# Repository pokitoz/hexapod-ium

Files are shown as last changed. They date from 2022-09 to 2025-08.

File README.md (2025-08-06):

# hexapod-ium

An hexapod robot using arduino and servo motors.
Manufacturing (PCB, 3D prints) and component assembly (PCBA) were done with PCBWay: https://www.pcbway.com/.




## Hardware

See the Kicad project in hw/ folder.

There is a Kicad Pluggin (https://www.pcbway.com/blog/News/PCBWay_Plug_In_for_KiCad_3ea6219c.html)
, 
simplifying the order process with PCBWay as the Gerber and BOM are filled in.

The design is reviewed and manufactured rapidely; which was very useful for this project.

### PCB

Kicad was used for the PCB design to add 2xPCA9865 and an ESP32.



### 3D Parts 

3D Printed parts can be done using a Prusa or Bamboo or any other 3d printer like the first iteration. 
But it was simpler to use PCBWay and the quality was better than printing on my own. The parameter used were:
- Resin Standard white material (UTR 8360)
- SLA

Design check and delivery was fast.



### Components

- 6x Leg (3 of them must be mirrored)
- 6x Holder
- 12 servo motors: MG90S or SG90 Micro Servo with screws
- 1 Arduino Uno
- PCA9865 (https://learn.adafruit.com/16-channel-pwm-servo-driver?view=all)
- Blu-tack
- Jumper cables

Need 5V for the motors board. VCC will be propagated to the main board (Arduino, ESP32,..)

You will need at least 2A upper limit to move all the motors at once.

## Software

### Arduino

Basic Arduino program to activate all the servo.
See the pinout in the .ino file. The VCC going out of the PCA9868 should go to the 5V of the board.

### ESP32

Might need driver https://www.silabs.com/developer-tools/usb-to-uart-bridge-vcp-drivers?tab=downloads

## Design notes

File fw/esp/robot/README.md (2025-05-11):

# ESP32 build

Use target: `esp32`, `ESP32-SOLO1-Module`.

Pinout:
- 3v3 and GND to PCA servo board
- SDA 21
- SCL 22



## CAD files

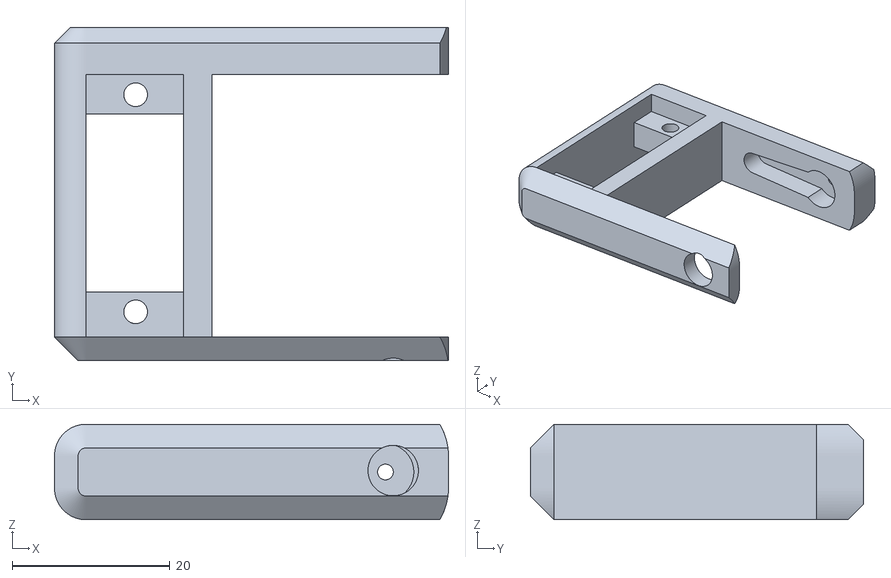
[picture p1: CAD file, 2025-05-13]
3d/Holder Leg.stl
50.0 x 42.3 x 12.1

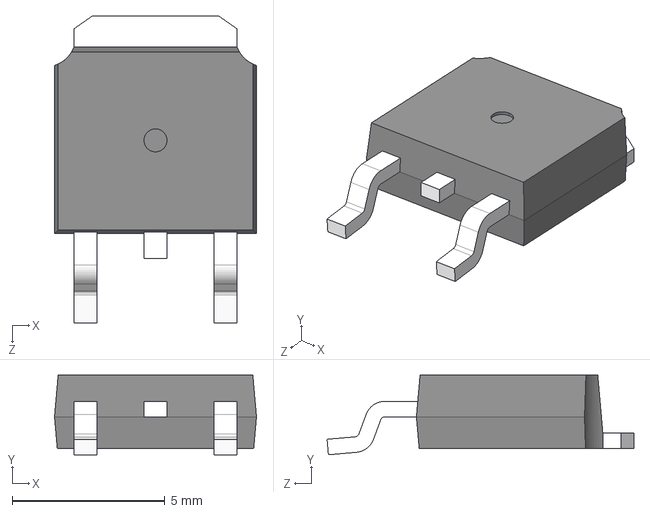
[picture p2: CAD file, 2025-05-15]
hw/AOD417/AOD417.step
6.60 x 2.60 x 10.0 mm

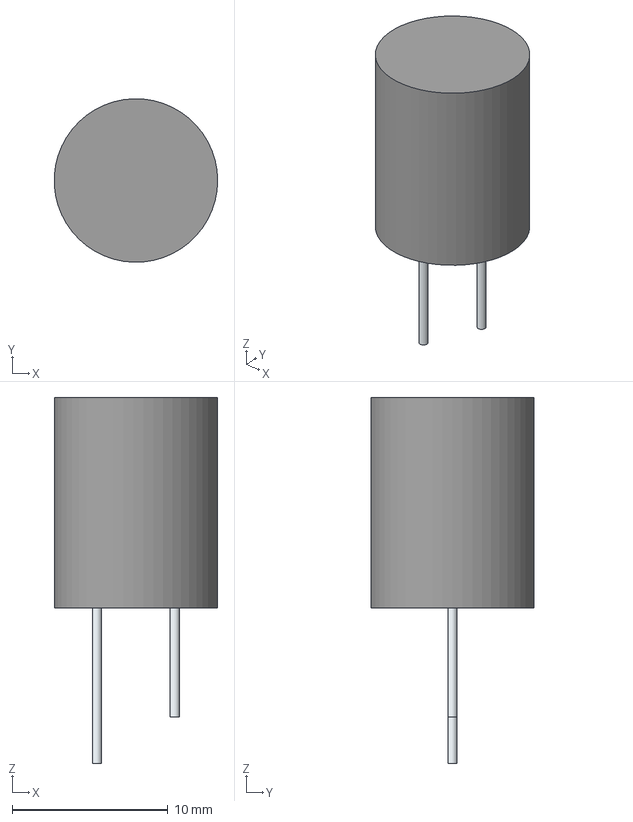
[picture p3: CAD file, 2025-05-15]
hw/ESH108M010AH1AA/3D/ESH108M010AH1AA.stp
10.5 x 10.5 x 23.5 mm
SimpleBody
Pin1
Pin2

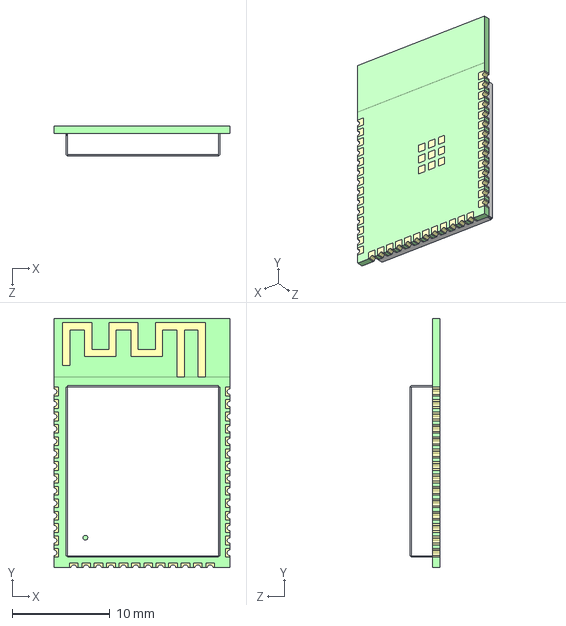
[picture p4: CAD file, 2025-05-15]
hw/ESP32-S3-WROOM-1-N8/3D/ESP32-S3-WROOM-1-N8.stp
18.0 x 25.5 x 3.10 mm

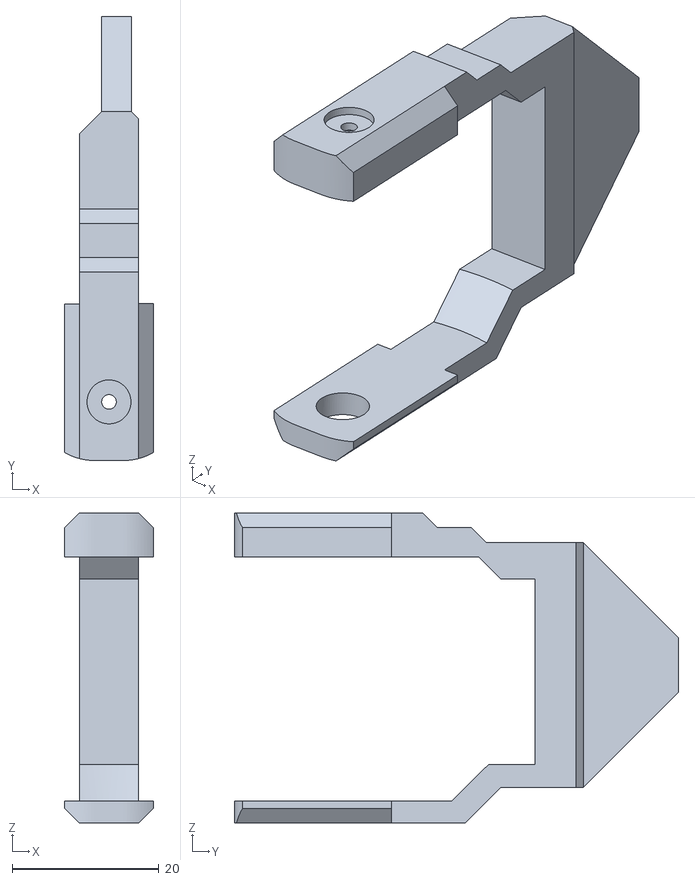
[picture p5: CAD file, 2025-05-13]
3d/Leg_v2.stl
12.1 x 60.6 x 42.3

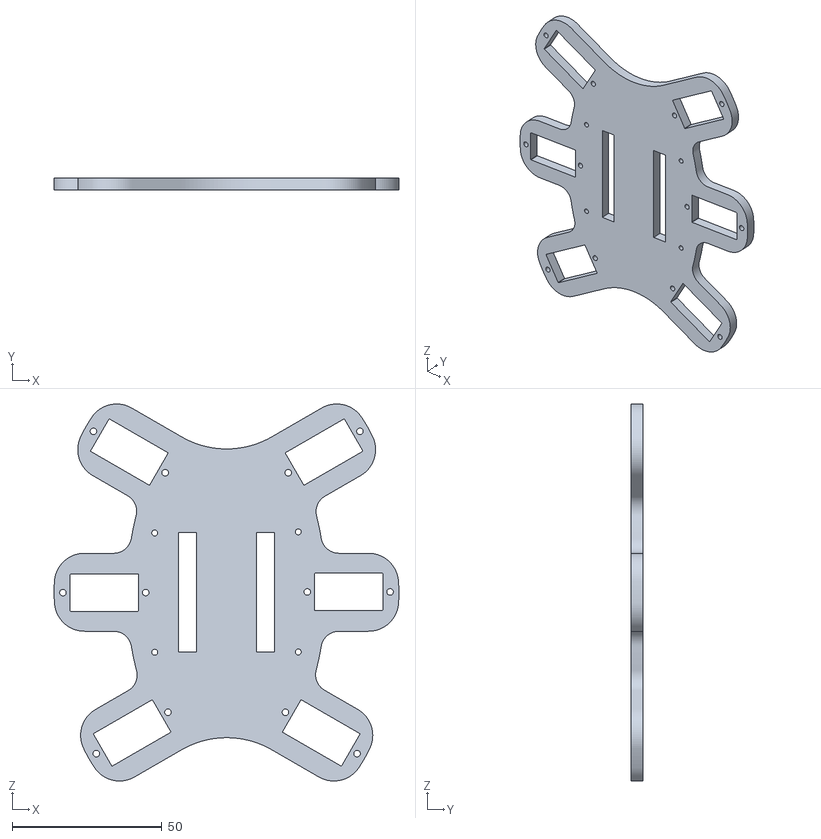
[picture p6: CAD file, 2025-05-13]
3d/BaseDown.stl
115.0 x 4.15 x 125.7

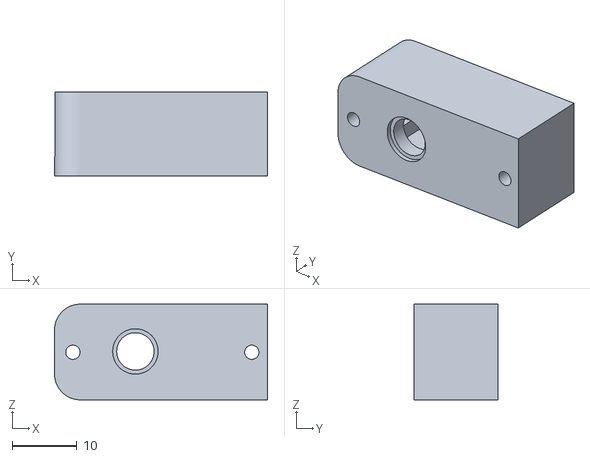
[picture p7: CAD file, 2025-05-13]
3d/ServoHat.stl
32.9 x 13.0 x 14.8

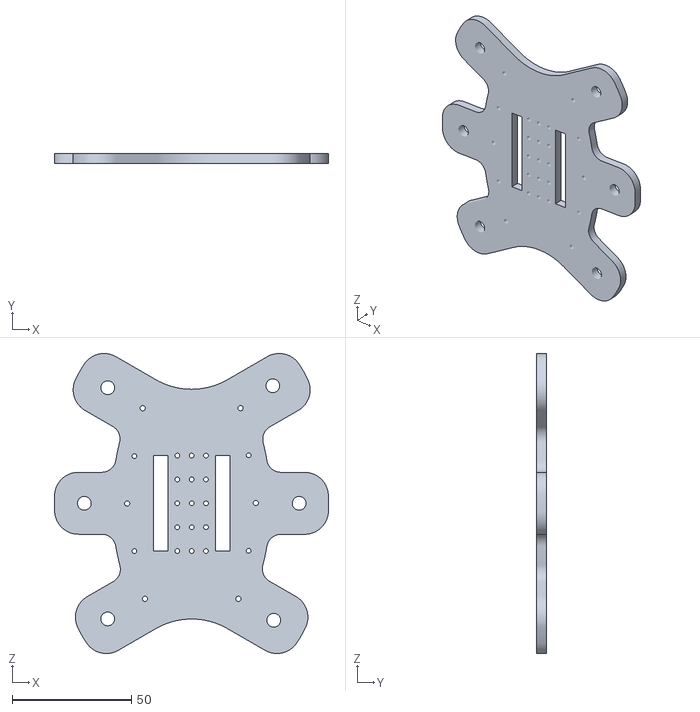
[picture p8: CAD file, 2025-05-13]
3d/Baseup.stl
115.0 x 4.15 x 125.7

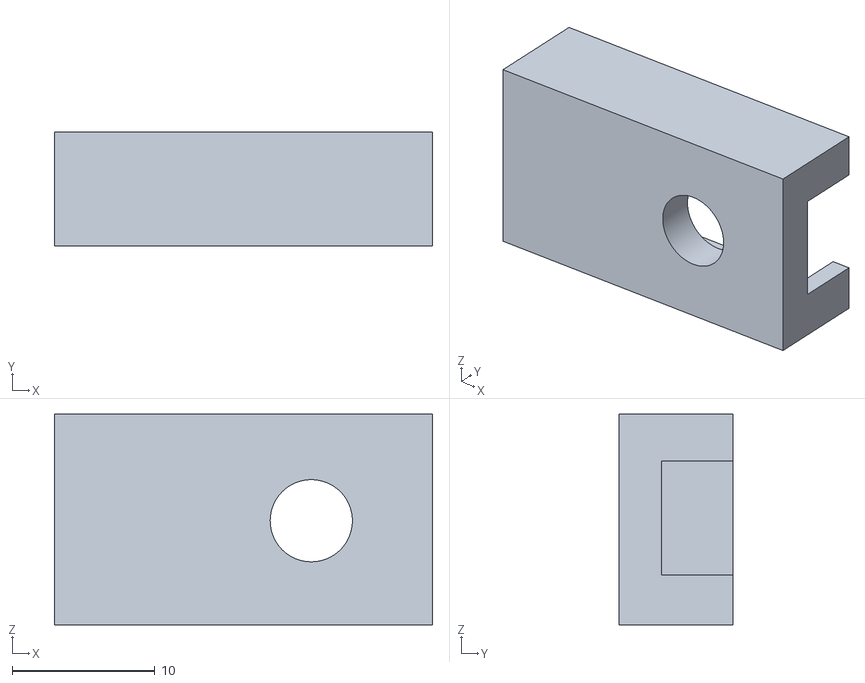
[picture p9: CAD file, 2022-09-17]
3d/Component1.stl
26.5 x 8.00 x 14.8

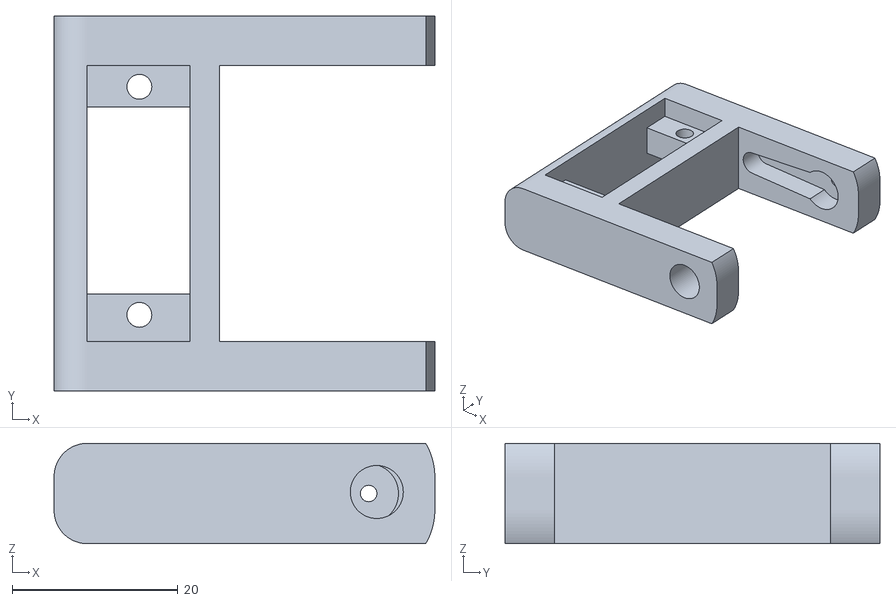
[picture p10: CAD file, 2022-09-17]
3d/Holder.stl
46.0 x 45.3 x 12.1

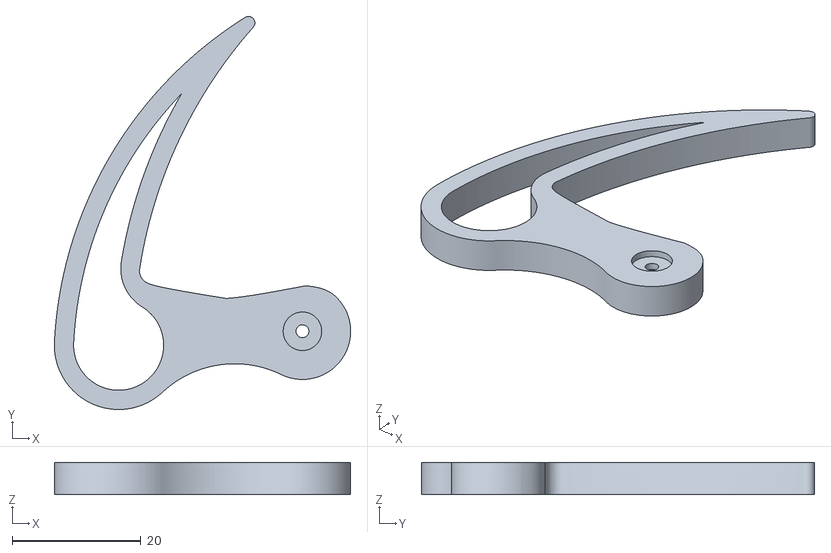
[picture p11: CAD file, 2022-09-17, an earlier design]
3d/Leg.stl
46.1 x 61.1 x 5.00

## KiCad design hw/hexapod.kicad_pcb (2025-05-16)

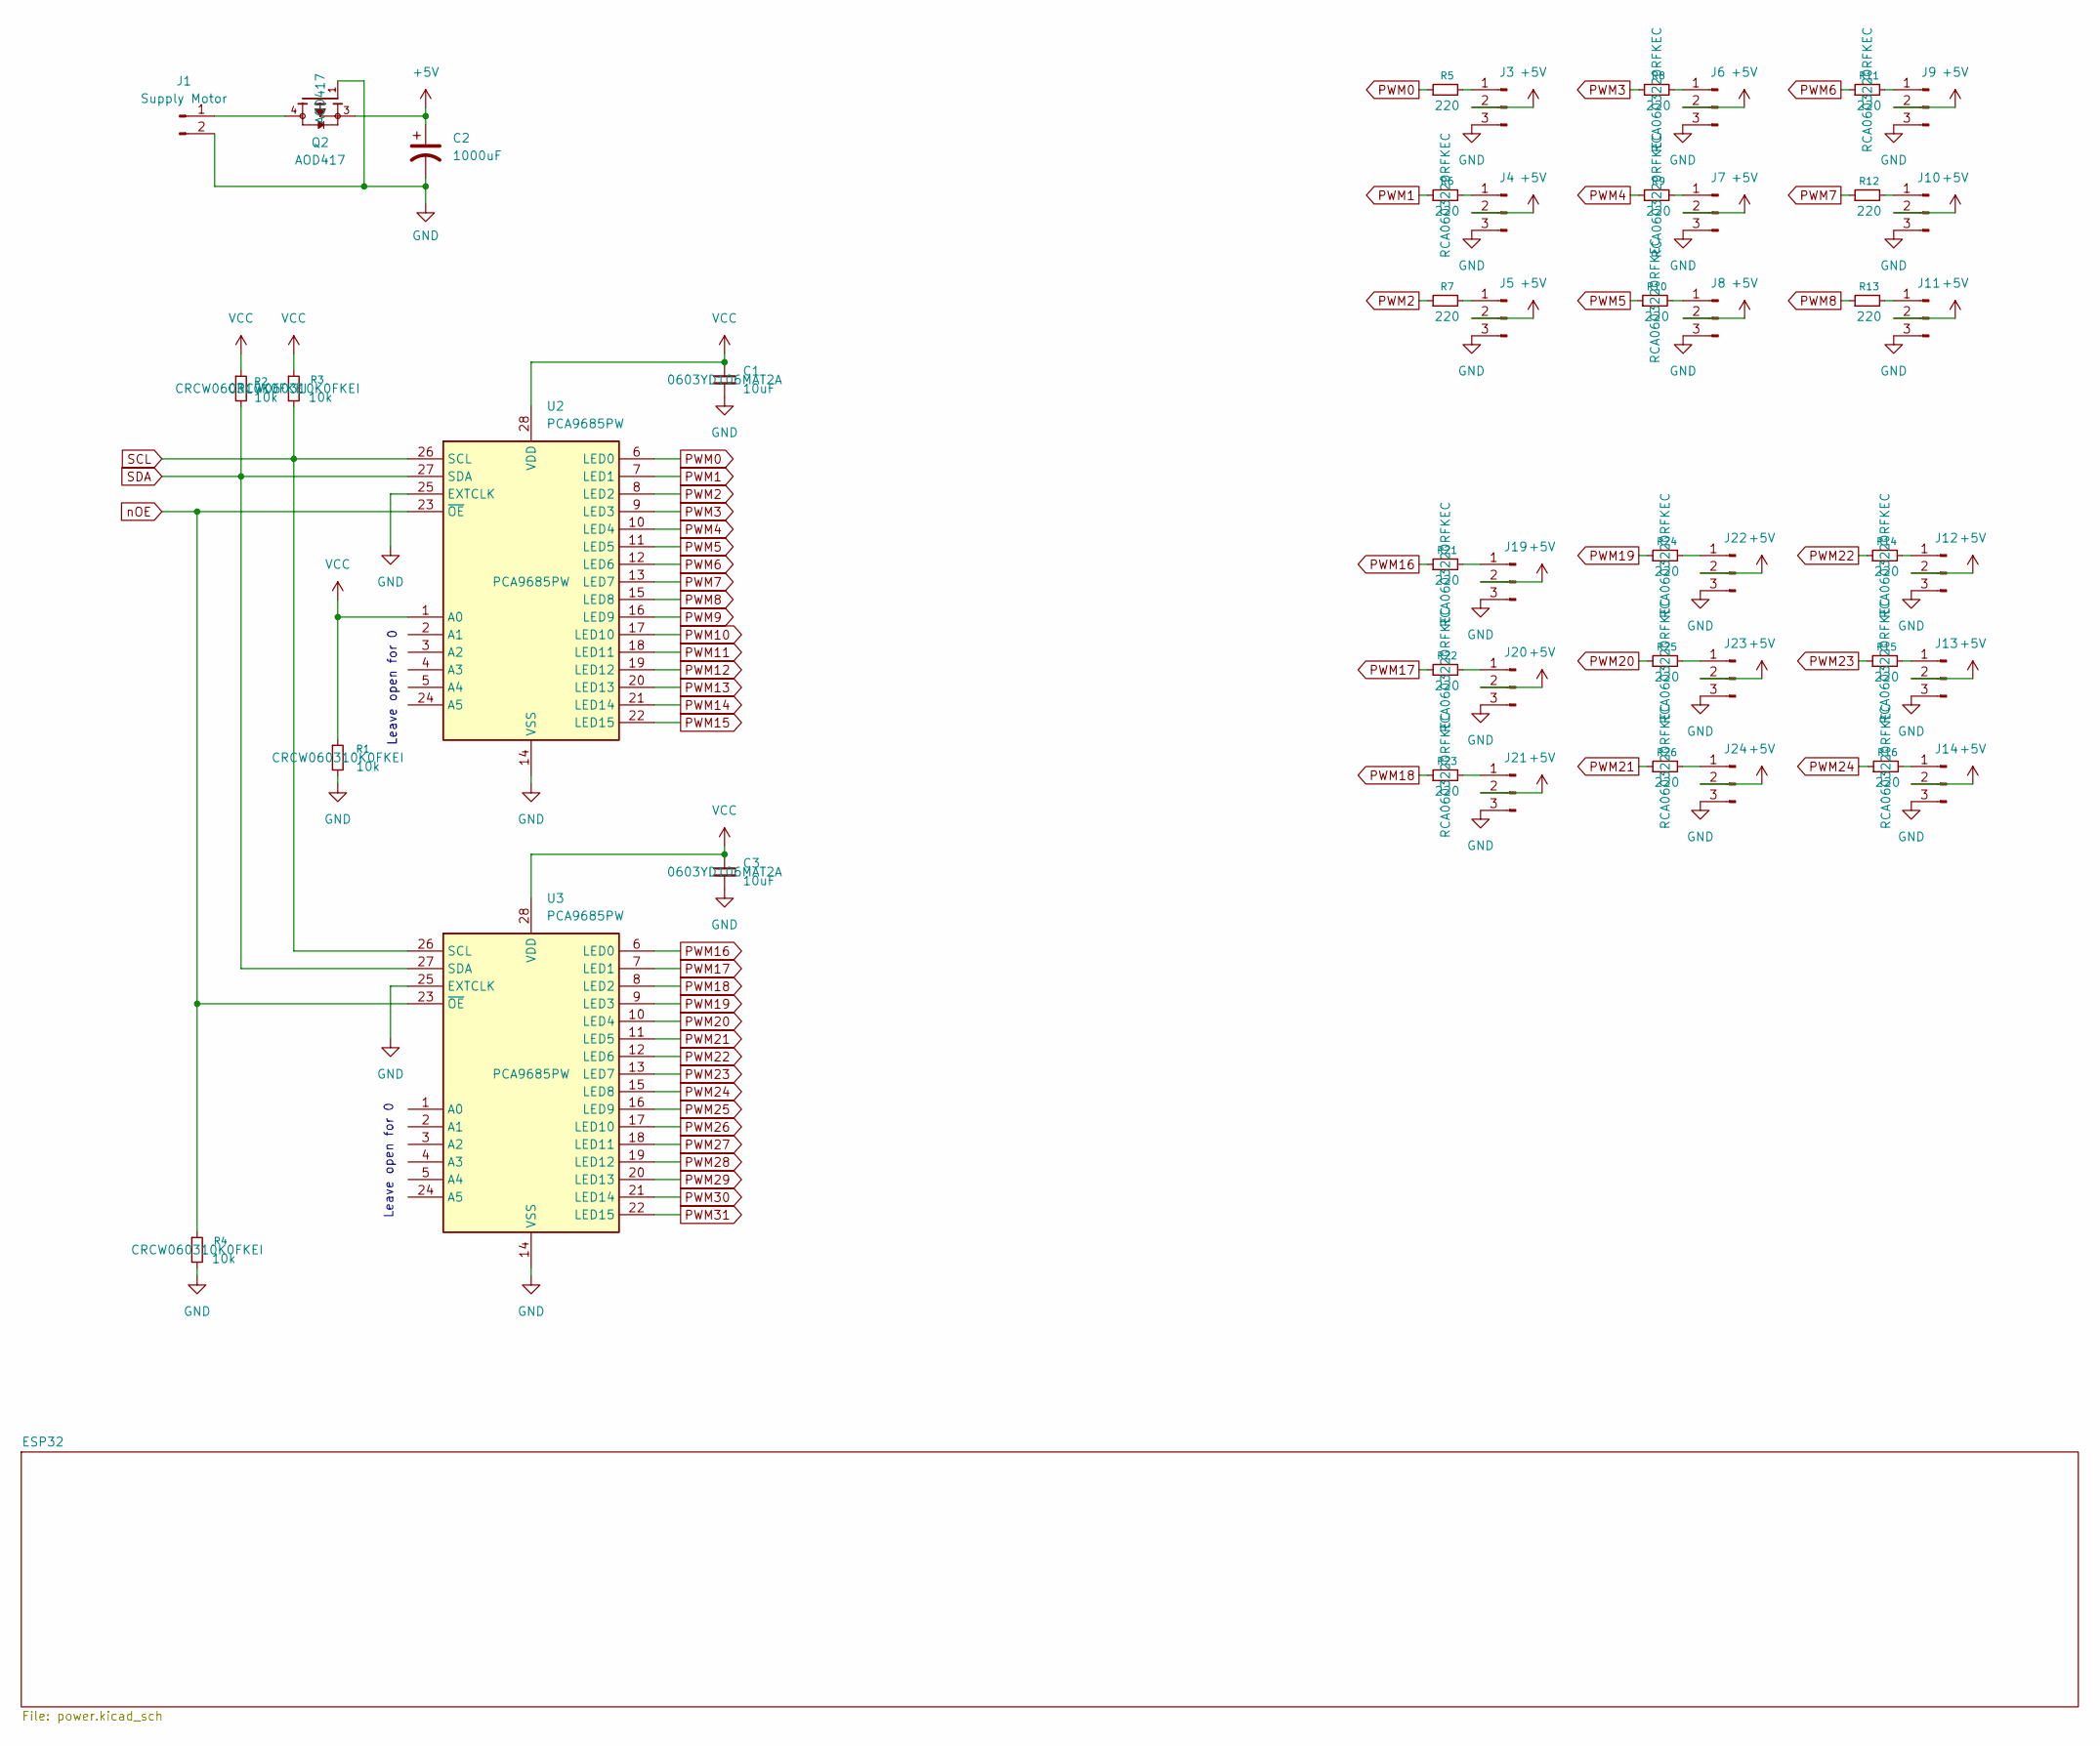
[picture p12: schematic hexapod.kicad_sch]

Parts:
C1, C3: 10uF; C_0603_1608Metric; Part 0603YD106MAT2A
C2: 1000uF; CAPPRD500W60D1000H1350
J1: Supply Motor; AMASS_XT30U-M_1x02_P5.0mm_Vertical
J3, J4, J5, J6, J7, J8, J9, J10, J11, J12, J13, J14, J19, J20, J21, J22, J23, J24: Conn_01x03_Pin; PinHeader_1x03_P2.54mm_Vertical
Q2: AOD417; DPAK228P994X240_3N; PARTREV U
R1, R2, R3, R4: 10k; R_0603_1608Metric_Pad0.98x0.95mm_HandSolder; Part CRCW060310K0FKEI
R5, R6, R7, R8, R9, R10, R11, R12, R13, R14, R15, R16, R21, R22, R23, R24, R25, R26: 220; R_0603_1608Metric_Pad0.98x0.95mm_HandSolder; Part RCA0603220RFKEC
U2, U3: PCA9685PW; TSSOP-28_4.4x9.7mm_P0.65mm; Part PCA9685PW

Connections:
+5V: C2.1, J3.2, J4.2, J5.2, J6.2, J7.2, J8.2, J9.2, J10.2, J11.2, J12.2, J13.2, J14.2, J19.2, J20.2, J21.2, J22.2, J23.2, J24.2, Q2.3
GND: C1.2, C2.2, C3.2, J1.2, J3.3, J4.3, J5.3, J6.3, J7.3, J8.3, J9.3, J10.3, J11.3, J12.3, J13.3, J14.3, J19.3, J20.3, J21.3, J22.3, J23.3, J24.3, Q2.1, R1.2, R4.2, U2.14 (VSS), U2.25 (EXTCLK), U3.14 (VSS), U3.25 (EXTCLK); also elsewhere on the board
unnamed: J1.1, Q2.4
unnamed: J3.1, R5.2
unnamed: J4.1, R6.2
unnamed: J5.1, R7.2
unnamed: J6.1, R8.2
unnamed: J7.1, R9.2
unnamed: J8.1, R10.2
unnamed: J9.1, R11.2
unnamed: J10.1, R12.2
unnamed: J11.1, R13.2
unnamed: J12.1, R14.2
unnamed: J13.1, R15.2
unnamed: J14.1, R16.2
unnamed: J19.1, R21.2
unnamed: J20.1, R22.2
unnamed: J21.1, R23.2
unnamed: J22.1, R24.2
unnamed: J23.1, R25.2
unnamed: J24.1, R26.2
PWM0: R5.1, U2.6 (LED0)
PWM1: R6.1, U2.7 (LED1)
PWM2: R7.1, U2.8 (LED2)
PWM3: R8.1, U2.9 (LED3)
PWM4: R9.1, U2.10 (LED4)
PWM5: R10.1, U2.11 (LED5)
PWM6: R11.1, U2.12 (LED6)
PWM7: R12.1, U2.13 (LED7)
PWM8: R13.1, U2.15 (LED8)
PWM9: U2.16 (LED9)
PWM10: U2.17 (LED10)
PWM11: U2.18 (LED11)
PWM12: U2.19 (LED12)
PWM13: U2.20 (LED13)
PWM14: U2.21 (LED14)
PWM15: U2.22 (LED15)
PWM16: R21.1, U3.6 (LED0)
PWM17: R22.1, U3.7 (LED1)
PWM18: R23.1, U3.8 (LED2)
PWM19: R24.1, U3.9 (LED3)
PWM20: R25.1, U3.10 (LED4)
PWM21: R26.1, U3.11 (LED5)
PWM22: R14.1, U3.12 (LED6)
PWM23: R15.1, U3.13 (LED7)
PWM24: R16.1, U3.15 (LED8)
PWM25: U3.16 (LED9)
PWM26: U3.17 (LED10)
PWM27: U3.18 (LED11)
PWM28: U3.19 (LED12)
PWM29: U3.20 (LED13)
PWM30: U3.21 (LED14)
PWM31: U3.22 (LED15)
SCL: R3.2, U2.26 (SCL), U3.26 (SCL); also elsewhere on the board
SDA: R2.2, U2.27 (SDA), U3.27 (SDA); also elsewhere on the board
VCC: C1.1, C3.1, R1.1, R2.1, R3.1, U2.1 (A0), U2.28 (VDD), U3.28 (VDD); also elsewhere on the board
nOE: R4.1, U2.23 (~OE), U3.23 (~OE)

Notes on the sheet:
Leave open for 0

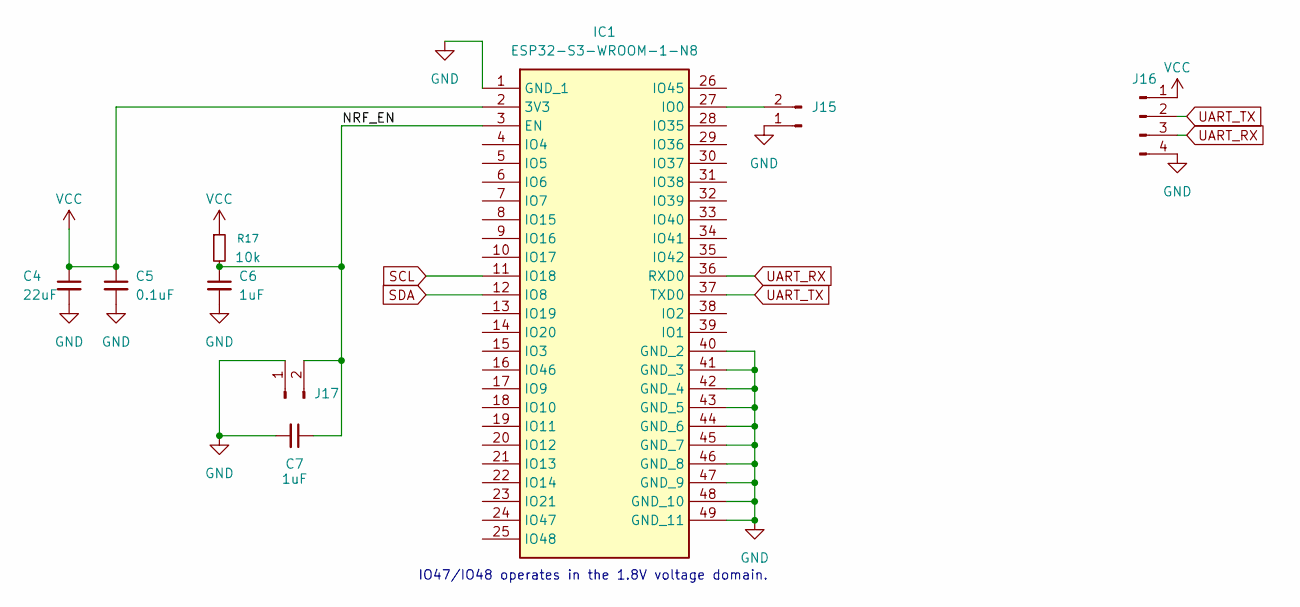
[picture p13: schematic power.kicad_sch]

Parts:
C4: 22uF; C_0603_1608Metric; Part 0603YD106MAT2A
C5: 0.1uF; C_0603_1608Metric; Part 0603YD106MAT2A
C6, C7: 1uF; C_0603_1608Metric; Part 0603YD106MAT2A
IC1: ESP32-S3-WROOM-1-N8; ESP32S3WROOM1N8R2; Mouser Part Number 356-ESP32-S3WROOM1N8
J15, J17: Conn_01x02_Pin; PinHeader_1x02_P2.54mm_Vertical
J16: Conn_01x04_Pin; PinHeader_1x04_P2.54mm_Vertical
R17: 10k; R_0603_1608Metric_Pad0.98x0.95mm_HandSolder; Part CRCW060310K0FKEI

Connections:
/ESP32/NRF_EN: C6.1, C7.1, IC1.3 (EN), J17.2, R17.2
GND: C4.2, C5.2, C6.2, C7.2, IC1.1 (GND_1), IC1.40 (GND_2), IC1.41 (GND_3), IC1.42 (GND_4), IC1.43 (GND_5), IC1.44 (GND_6), IC1.45 (GND_7), IC1.46 (GND_8), IC1.47 (GND_9), IC1.48 (GND_10), IC1.49 (GND_11), J15.1, J16.4, J17.1; also elsewhere on the board
unnamed: IC1.27 (IO0), J15.2
SCL: IC1.11 (IO18); also elsewhere on the board
SDA: IC1.12 (IO8); also elsewhere on the board
UART_RX: IC1.36 (RXD0), J16.3
UART_TX: IC1.37 (TXD0), J16.2
VCC: C4.1, C5.1, IC1.2 (3V3), J16.1, R17.1; also elsewhere on the board

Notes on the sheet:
IO47/IO48 operates in the 1.8V voltage domain.

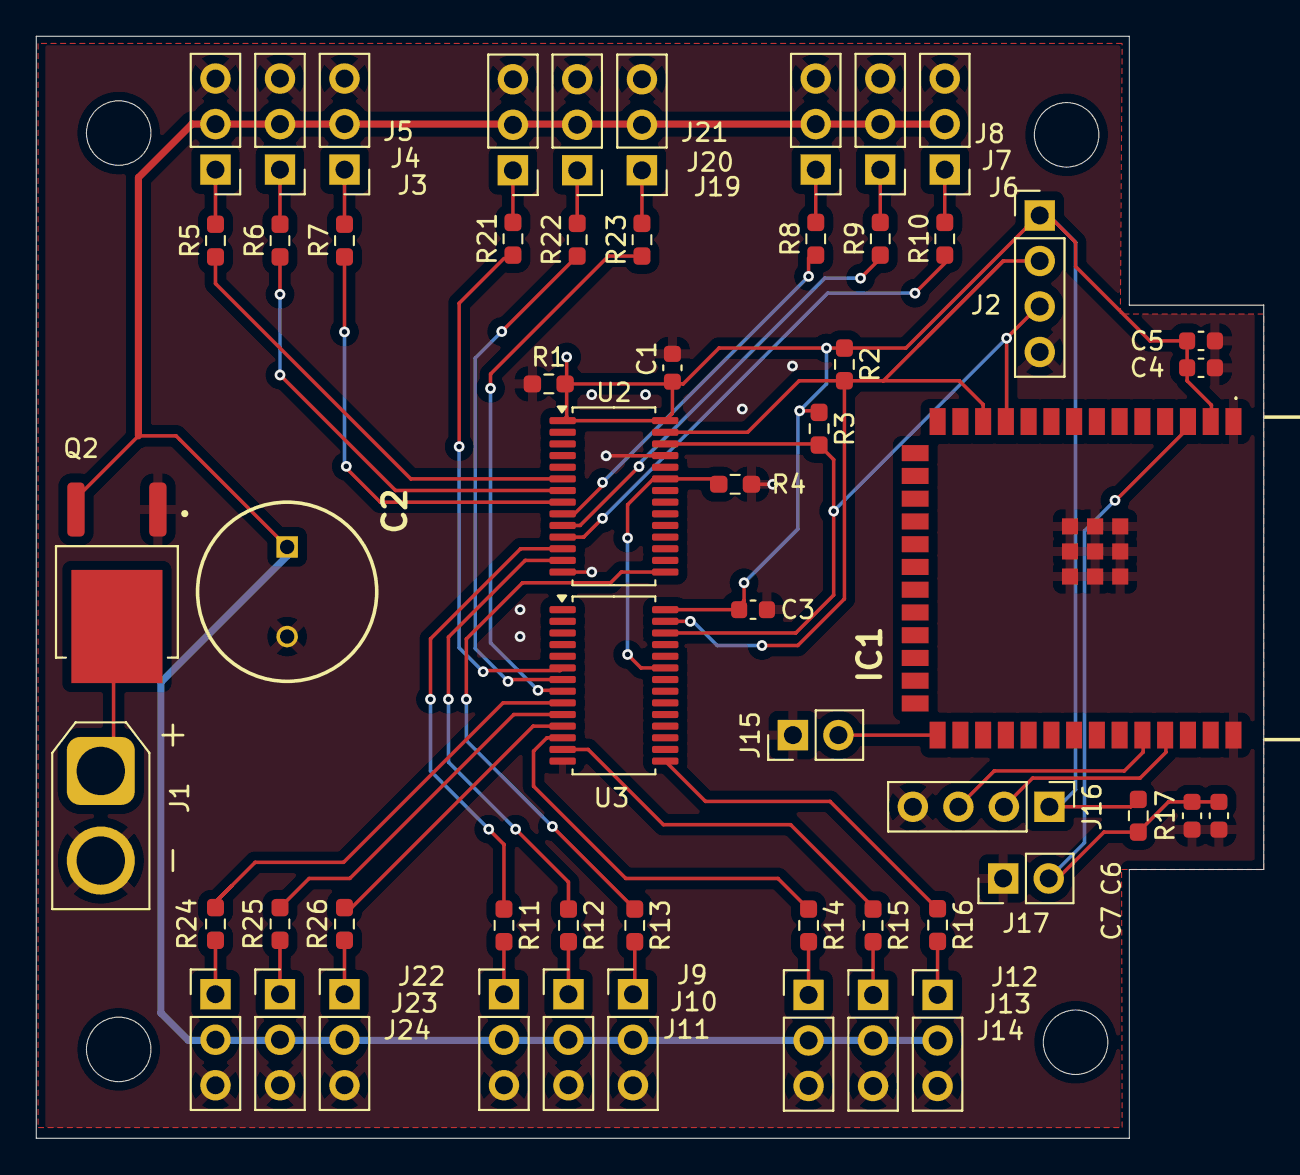
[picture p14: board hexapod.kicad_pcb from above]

Board: 2 copper layers, 68.5 x 61.5 mm, 57 parts (0 on the bottom side), 47 nets.

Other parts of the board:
J2: Conn_01x04_Pin; PinHeader_1x04_P2.54mm_Vertical

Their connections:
GND: J2.4; also elsewhere on the board
SCL: J2.3; also elsewhere on the board
SDA: J2.2; also elsewhere on the board
VCC: J2.1; also elsewhere on the board

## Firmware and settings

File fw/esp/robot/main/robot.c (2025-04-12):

/**
 * @file pca9685_servo_controller.c
 * @brief ESP32-based PCA9685 servo control via I2C using FreeRTOS.
 *
 * This code initializes the I2C master and configures the PCA9685 PWM driver
 * to control multiple servo motors with different motion patterns.
 */

#include <string.h>
#include "freertos/FreeRTOS.h"
#include "freertos/task.h"
#include "esp_system.h"
#include "esp_log.h"
#include "nvs_flash.h"
#include "driver/i2c.h"
#include "esp_err.h"

// I2C configuration
#define I2C_MASTER_NUM I2C_NUM_0
#define I2C_MASTER_SDA_IO 21
#define I2C_MASTER_SCL_IO 22
#define I2C_MASTER_FREQ_HZ 100000

// PCA9685 configuration
#define PCA9685_ADDR 0x40
#define PCA9685_MODE1 0x00
#define PCA9685_PRESCALE 0xFE
#define SERVO_FREQ 50

// PWM bounds for servo
#define SERVO_MIN 100
#define SERVO_MAX 475

static const char *TAG = "PCA9685_SERVO";

/**
 * @struct ServoConfig
 * @brief Configuration parameters for a single servo channel.
 */
typedef struct
{
    uint8_t channelID;
    uint32_t max;
    uint32_t min;
    uint32_t mid;
} ServoConfig;

// Leg servo configurations
static const ServoConfig legs[] = {
    {1, SERVO_MAX, SERVO_MIN - 30, 185},
    {4, SERVO_MAX + 30, SERVO_MIN, 300},
    {5, SERVO_MAX, SERVO_MIN - 30, 200},
    {7, SERVO_MAX, SERVO_MIN, 200},
    {15, SERVO_MAX + 30, SERVO_MIN, 310},
    {11, SERVO_MAX + 30, SERVO_MIN, 220},
};

// Mid servo configurations
static const ServoConfig mids[] = {
    {2, 300, 0, 220},
    {3, 270, 0, 220},
    {6, 270, 0, 220},
    {8, 270, 0, 120},
    {10, 250, 0, 280},
    {12, 110, 0, 180},
};

static const uint32_t numLegs = sizeof(legs) / sizeof(ServoConfig);
static const uint32_t numMids = sizeof(mids) / sizeof(ServoConfig);

/**
 * @brief Initialize I2C as master.
 */
void i2cMasterInit(void)
{
    const i2c_config_t conf = {
        .mode = I2C_MODE_MASTER,
        .sda_io_num = I2C_MASTER_SDA_IO,
        .scl_io_num = I2C_MASTER_SCL_IO,
        .sda_pullup_en = GPIO_PULLUP_DISABLE,
        .scl_pullup_en = GPIO_PULLUP_DISABLE,
        .master.clk_speed = I2C_MASTER_FREQ_HZ,
    };

    ESP_ERROR_CHECK(i2c_param_config(I2C_MASTER_NUM, &conf));
    ESP_ERROR_CHECK(i2c_driver_install(I2C_MASTER_NUM, conf.mode, 0, 0, 0));
}

/**
 * @brief Write a single byte to PCA9685 register.
 */
void pca9685WriteByte(uint8_t reg, uint8_t data)
{
    const uint8_t buf[] = {reg, data};
    ESP_ERROR_CHECK(i2c_master_write_to_device(I2C_MASTER_NUM, PCA9685_ADDR, buf, sizeof(buf), 1000 / portTICK_PERIOD_MS));
}

/**
 * @brief Set PWM value for a channel.
 */
void pca9685SetPWM(uint8_t channel, uint16_t on, uint16_t off)
{
    const uint8_t buf[] = {
        0x06 + (4 * channel),
        on & 0xFF,
        (on >> 8) & 0xFF,
        off & 0xFF,
        (off >> 8) & 0xFF};
    ESP_ERROR_CHECK(i2c_master_write_to_device(I2C_MASTER_NUM, PCA9685_ADDR, buf, sizeof(buf), 1000 / portTICK_PERIOD_MS));
}

/**
 * @brief Initialize PCA9685 module.
 */
void pca9685Init(void)
{
    pca9685WriteByte(PCA9685_MODE1, 0x10); // Sleep
    uint8_t prescale = (uint8_t)(25000000 / (4096 * SERVO_FREQ) - 1);
    pca9685WriteByte(PCA9685_PRESCALE, prescale);
    pca9685WriteByte(PCA9685_MODE1, 0xA0); // Restart and normal mode
}

// --- Leg control helpers ---

void legUp(int id)
{
    pca9685SetPWM(legs[id].channelID, 0, legs[id].max);
}

void legDown(int id)
{
    pca9685SetPWM(legs[id].channelID, 0, legs[id].min);
}

void legMid(int id)
{
    pca9685SetPWM(legs[id].channelID, 0, legs[id].mid);
}

void midMid(int id)
{
    pca9685SetPWM(mids[id].channelID, 0, mids[id].mid);
}

void midMax(int id)
{
    pca9685SetPWM(mids[id].channelID, 0, mids[id].max);
}

/**
 * @brief Main app entry point. Drives servo animations in loop.
 */
void app_main(void)
{
    // Initialize NVS
    esp_err_t ret = nvs_flash_init();
    if (ret == ESP_ERR_NVS_NO_FREE_PAGES || ret == ESP_ERR_NVS_NEW_VERSION_FOUND)
    {
        ESP_ERROR_CHECK(nvs_flash_erase());
        ESP_ERROR_CHECK(nvs_flash_init());
    }

    ESP_LOGI(TAG, "Initializing I2C and PCA9685...");
    i2cMasterInit();
    pca9685Init();

    const uint32_t setupDelay = 1500;

    while (1)
    {
        for (int i = 0; i < numMids; i++)
            midMax(i);

        for (int i = 0; i < numLegs; i++)
        {
            if (i % 2)
            {
                legUp(i);
                midMax(i);
            }
            else
            {
                legMid(i);
                midMid(i);
            }
        }

        vTaskDelay(setupDelay / portTICK_PERIOD_MS);

        for (int i = 0; i < numLegs; i++)
            legMid(i);
        vTaskDelay(setupDelay / portTICK_PERIOD_MS);

        for (int i = 0; i < numLegs; i++)
        {
            if (i % 2)
            {
                legMid(i);
                midMid(i);
            }
            else
            {
                legUp(i);
                midMax(i);
            }
        }

        vTaskDelay(setupDelay / portTICK_PERIOD_MS);
        for (int i = 0; i < numLegs; i++)
            legMid(i);
        vTaskDelay(setupDelay / portTICK_PERIOD_MS);
    }
}

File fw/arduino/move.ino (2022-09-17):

#include <Wire.h>
#include <Adafruit_PWMServoDriver.h>

Adafruit_PWMServoDriver pwm = Adafruit_PWMServoDriver();
#define C_SERVO_MIN  100
#define C_SERVO_MAX  475
#define SERVO_FREQ 50

void setup() {
  Serial.begin(9600);
  pwm.begin();
  pwm.setPWMFreq(SERVO_FREQ); 
  delay(10);
}

int servoLeg [] = {1, 4, 5, 7, 15, 11};
int servoMax [] = {C_SERVO_MAX, C_SERVO_MAX + 30, C_SERVO_MAX,      C_SERVO_MAX, C_SERVO_MAX + 30, C_SERVO_MAX + 30};
int servoMin [] = {C_SERVO_MIN - 30, C_SERVO_MIN, C_SERVO_MIN - 20, C_SERVO_MIN, C_SERVO_MIN     , C_SERVO_MIN };
int servoHalf [] = {185, 300, 200, 200, 310, 220};

int servoMid [] = {2, 3, 6, 8, 10, 12};
int servoMidVal[] = {300, 270, 270, 140, 250, 110};
int servoMidValInc[] = {220, 220, 220, 120, 280, 180};

int sizeServo = 6;
int sizeServoMid = 6;

void legUp(int id)
{
  if (id <= 2)
  {
    pwm.setPWM(servoLeg[id], 0, servoMax[id]);
  }
  else
  {
    pwm.setPWM(servoLeg[id], 0, servoMin[id]);
  }
}

void legDown(int id)
{
  if (id <= 2)
  {
    pwm.setPWM(servoLeg[id], 0, servoMin[id]);
  }
  else
  {
    pwm.setPWM(servoLeg[id], 0, servoMax[id]);
  }
}

void legHalf(int id)
{
  pwm.setPWM(servoLeg[id], 0, servoHalf[id]);
}

void legMiddle(int id)
{
  pwm.setPWM(servoMid[id], 0, servoMidVal[id]);
}

void legInc(int id)
{
  pwm.setPWM(servoMid[id], 0, servoMidValInc[id]);
}

void loop() {
    for (int i = 0; i < sizeServoMid; i++)
    {
      legInc(i);
    }

    for (int i = 0; i < sizeServo; i++) {
      if (i % 2)
      {
        legUp(i);
        legInc(i);
      }
      else
      {
        legHalf(i);
        legMiddle(i);
      }
    }

    delay(1000);
    for (int i = 0; i < sizeServo; i++) {
        legHalf(i);
    }

    delay(1000);

    for (int i = 0; i < sizeServo; i++) {

      if (i % 2)
      {
        legHalf(i);
        legMiddle(i);
      }
      else
      {
        legUp(i);
        legInc(i);
      }
    }

    delay(1000);
    for (int i = 0; i < sizeServo; i++) {
      legHalf(i);
    }

    delay(1000);
}

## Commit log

2022-09-17 Add 3d Print files
    [BaseDown.stl, Baseup.stl, Component1.stl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]
2022-09-17 Add ugly but working arduino code
2025-04-12 Add ESP build
    [BaseDown.stl, Baseup.stl, Component1.stl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]
2025-04-12 Refactor esp32 code
2025-05-11 Add picture ESP32
2025-05-13 Update STL
    [BaseDown.stl, Baseup.stl, Holder Leg.stl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]
2025-05-15 Add HW files for motor pwm
    [AOD417.step, ESH108M010AH1AA.stp, hexapod.kicad_pcb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]
2025-05-15 hw: Keep only needed pwm
    [ESP32-S3-WROOM-1-N8.stp, hexapod.kicad_pcb, hexapod.kicad_sch]
2025-05-16 hw: Add ESP32
    [hexapod.kicad_pcb, hexapod.kicad_sch, power.kicad_sch]
2025-07-26 readme: add link to kicad plugin for PCBWay
2025-07-26 readme: Add picture from PCBWay manufacturing
2025-08-06 Add more details about PCBWay order
